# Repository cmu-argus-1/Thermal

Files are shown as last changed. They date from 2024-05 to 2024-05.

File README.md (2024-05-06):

# Thermal
All files relating the thermal management of Argus-1 are located here. The following files can located within this repository:
* Thermal Desktop setup and login information
* Thermal Desktop help manuals and tutorials
* Argus-1 Thermal Desktop files
* Argus-1 TVAC test plan
* Argus-1 thermal management system CAD files
* Argus-1 thermal strap DXF files

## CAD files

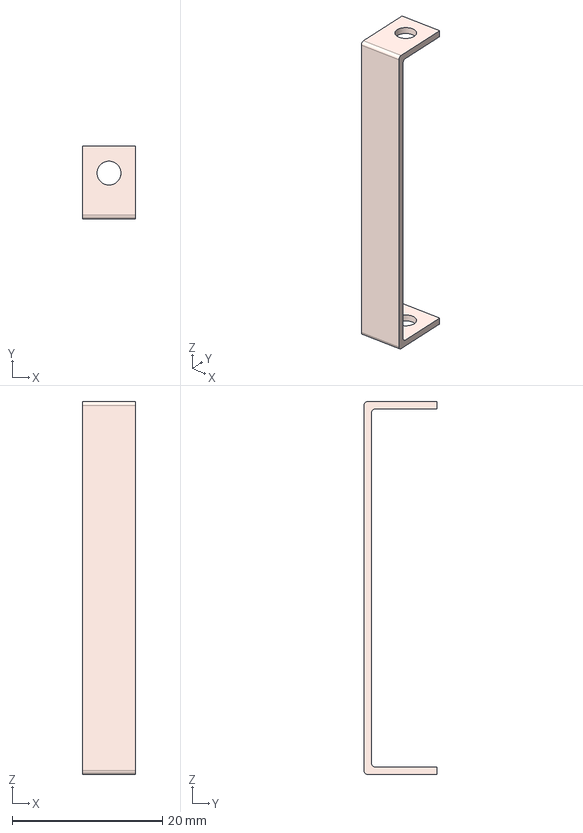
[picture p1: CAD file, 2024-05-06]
Thermal Strap Short.step
7.00 x 9.70 x 49.6 mm

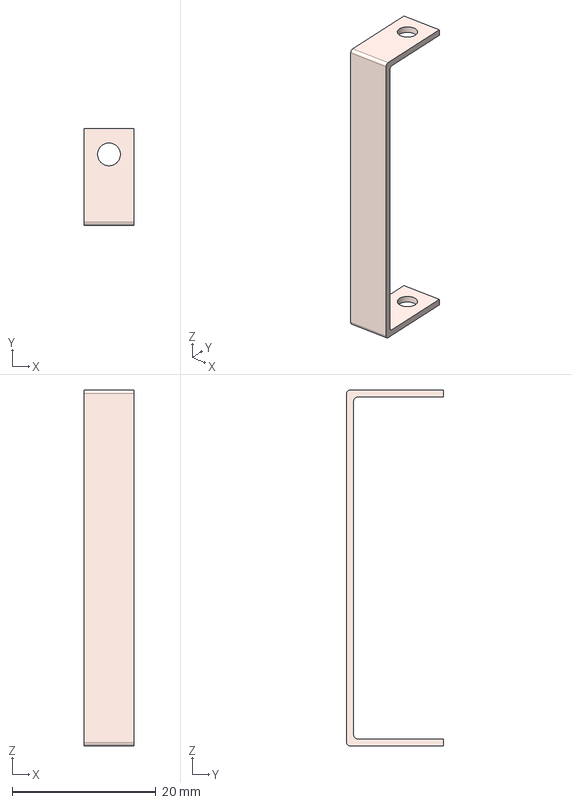
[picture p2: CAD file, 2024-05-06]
Thermal Strap Long.step
7.00 x 13.5 x 49.6 mm

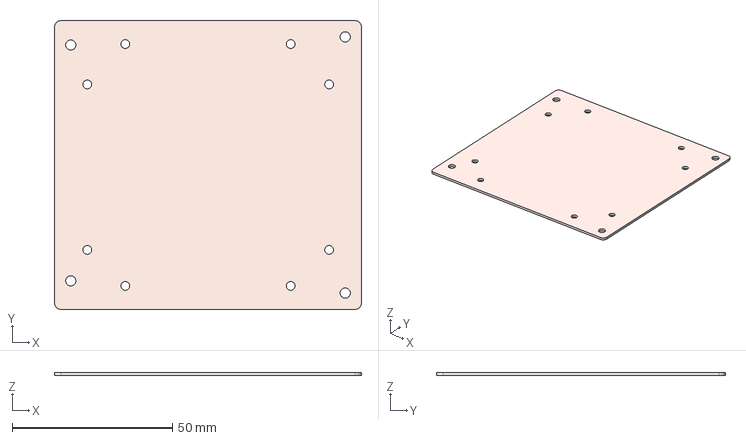
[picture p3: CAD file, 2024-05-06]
Jetson Thermal Sink Board.step
95.9 x 90.2 x 1.00 mm

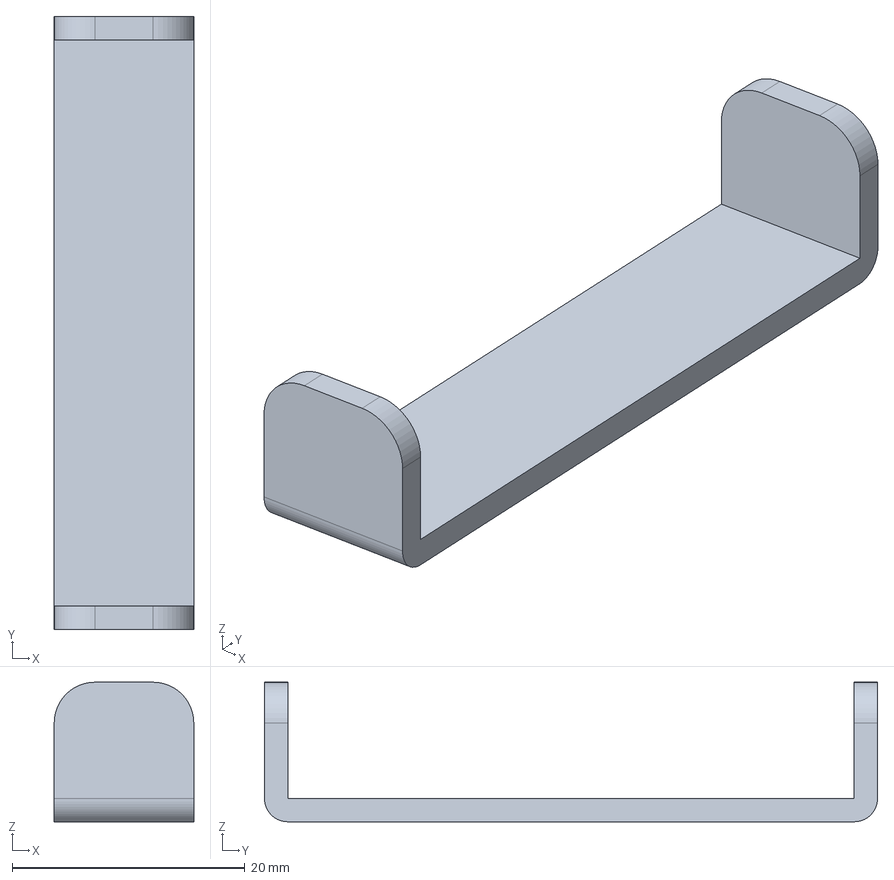
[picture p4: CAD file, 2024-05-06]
Copper Strap.step
12.0 x 52.7 x 12.0 mm

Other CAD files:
TDD_Test_Drawing.dwg
CubeSat_v1.dwg

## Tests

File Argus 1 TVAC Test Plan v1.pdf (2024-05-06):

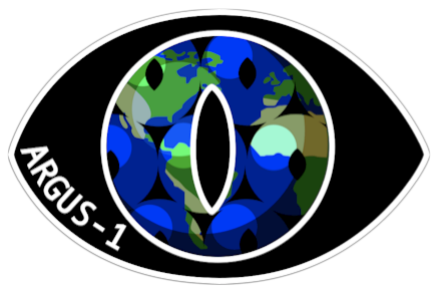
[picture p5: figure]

# Argus-1

# Camera Module Endurance

&

# Jetson Thermal Management TVAC Test Plan

Carnegie Mellon University 5000 Forbes Ave
Pittsburgh, PA 15213
Revision | Release Notes Author | Release Date
A | Initial Release Colton Amos | 4/11/2024

Revision | Title | Release Date | Page
A | Camera Module and Jetson TVAC Test Plan | 4/11/2024 | 2 of 19

Table of Contents
Page No.
1.0 Purpose and Scope | 3
2.0 (https://docs.google.com/document/d/1Rzob_Sl6tvCRn7rMNGoZeeShy_QEGQafTcheLyu6lXM/edit) Involved Personnel | 5
3.0 Test Articles | 6
4.0 Facilities | | | 7
5.0 Test Procedures | 11
6.0 Results & Conclusions | 16
7.0 Literature and Relevant Documents | 22

A | Camera Module and Jetson TVAC Test Plan | 4/11/2024 | 3 of 19

### 1.0 Purpose and Scope

This test plan verifies the endurance capabilities of a selected camera unit and its consequent resistance to thermal distortion in its lenses and mounted PCB. Furthermore, this plan will also investigate the proficiency of a proposed thermal management system for an on board Jetson unit. The performance of a copper vs aluminum thermal sink board will be compared utilizing a copper thermal strap to the aluminum chassis. These results and their respective conductances will then be incorporated into a protoflight thermal model.

1.1 Requirements Table

Table 1: Requirements
ID | Title | Description | Information Learned in this Version
THR-01 | Survival Temperature Regulation | The thermal system shall maintain temperatures in accordance with the ThEL survival temperatures during orbit without operating high-risk avionics components.
THR-02 | Operation Temperature Regulation | The thermal system shall maintain temperatures in accordance with the ThEL operating temperatures during orbit that involve high-risk components being on.
THR-17 | Thermal Model Correlation | Argus-1 shall have a thermal model that is correlated to within 5% temperature accuracy in K.
THR-18 | Thermal Vacuum Survivability | The thermal system shall use components that will survive the vacuum conditions of low Earth orbit.

A | Camera Module and Jetson TVAC Test Plan | 4/11/2024 | 4 of 19

### 2.0 Involved Personnel

Table 2: Personnel
Name | Role | Contact Information
Colton Amos | Thermal Lead | camos@andrew.cmu.edu
Ashley Kline | Mechanical Engineer | ankline@andrew.cmu.edu
Allison Weller | Mechanical Engineer | ahweller@andrew.cmu.edu
Sankalp Chopkar | Mechanical Engineer | schopkar@andrew.cmu.edu
Rohit Bangal | Avionics Engineer | rbangal@andrew.cmu.edu
Elakhya Nedumaran | Payload Engineer | enedumar@andrew.cmu.edu
Paulo Fisch | Thermal/Mechanical Advisor | pfisch@andrew.cmu.edu
Zach Manchester | Professor | zmanches@andrew.cmu.edu
Brandon Lucia | Professor | blucia@andrew.cmu.edu
Chuck Whittaker | Supervisor | warrenw@andrew.cmu.edu

A | Camera Module and Jetson TVAC Test Plan | 4/11/2024 | 5 of 19

### 3.0 Test Articles

The TVAC test will be primarily testing two articles. A fully assembled Arducam camera module including its two mounted PCB’s, its camera housing and its camera lens. A CAD representation of this article can be found below:

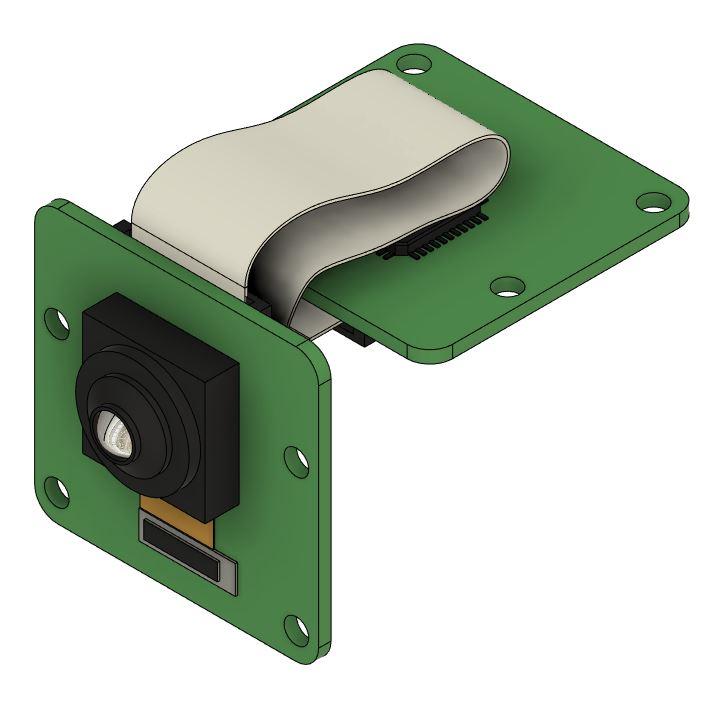
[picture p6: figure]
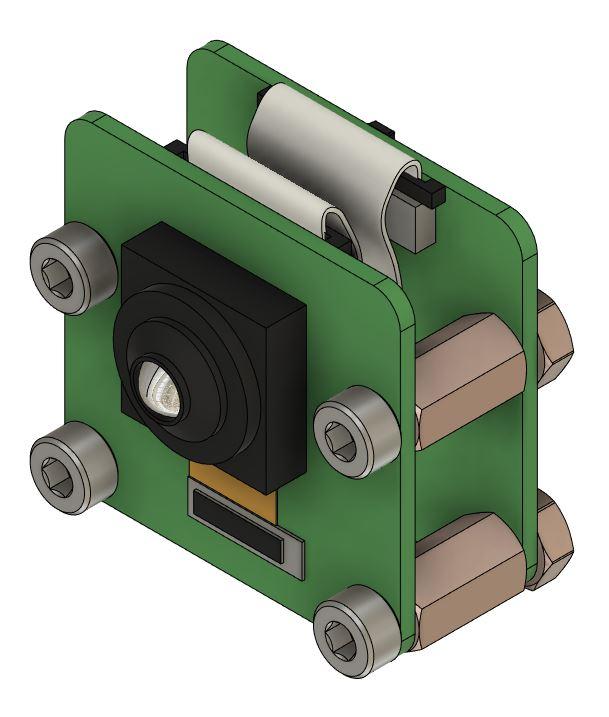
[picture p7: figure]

The second test article will be sub assembly of the thermal management system for the Jetson Module. This sub assembly includes: the chassis frame and legs, M3 PC104 rods, 4 copper thermal straps, a copper and aluminum thermal sink board, a Jetson Module, Jetson carrier board, thermal gap pad, and all associated M3 mounting hardware. Abbreviated assembly instructions can be found in Table 4: Test Setup. A CAD representation of the thermal management system can be found below:

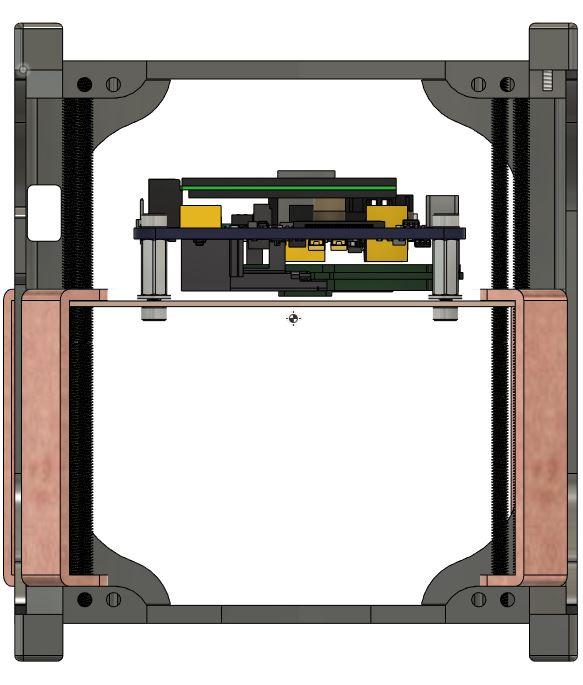
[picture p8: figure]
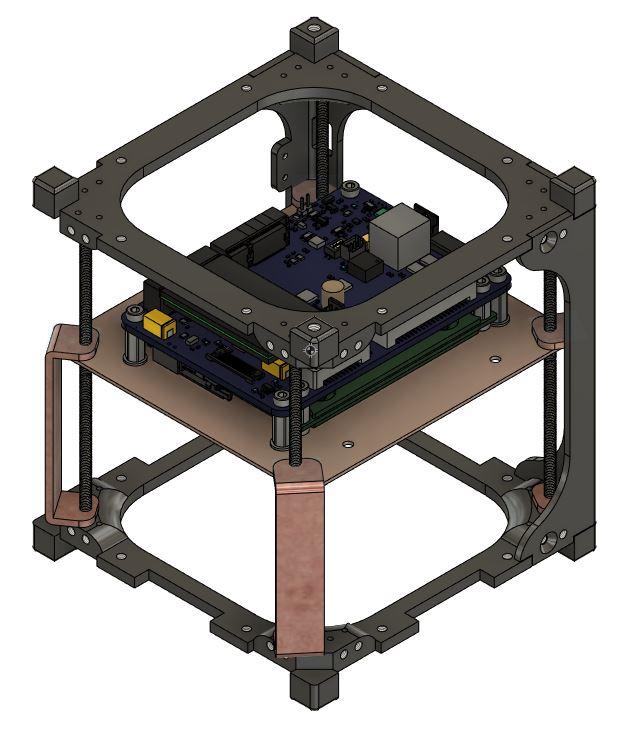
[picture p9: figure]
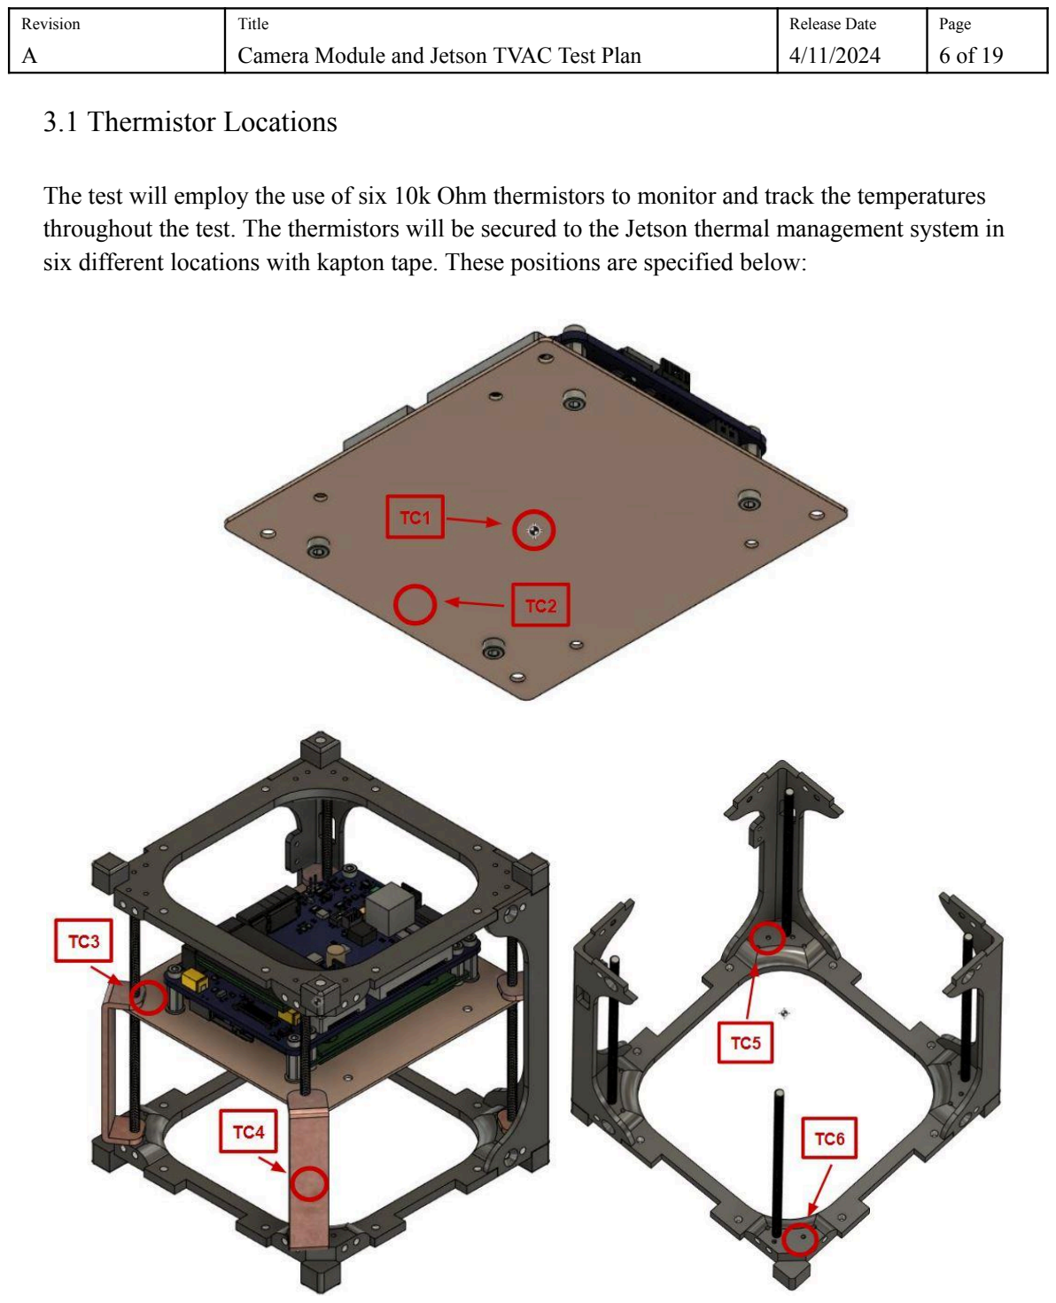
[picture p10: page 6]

A | Camera Module and Jetson TVAC Test Plan | 4/11/2024 | 6 of 19

3.1 Thermistor Locations

The test will employ the use of six 10k Ohm thermistors to monitor and track the temperatures throughout the test. The thermistors will be secured to the Jetson thermal management system in six different locations with kapton tape. These positions are specified below:

A | Camera Module and Jetson TVAC Test Plan | 4/11/2024 | 7 of 19

### 4.0 Facilities

The test will happen in the Robotics Institutes’s vacuum chamber, located in the Planetary Robotics Laboratory High Bay on floor 1 of Gates Center.

### 5.0 Test Procedures

5.1 Summary

Table 3: Summary
Description:

This test assesses the effects of thermal dilation of a camera unit and a Jetson computing unit under TVAC conditions. The camera module’s PCB and lens resistance to thermal distortion are going to be measured by placing a fully assembled camera module onto the bottom of the vacuum chamber’s cryogenic shroud, which will cool the camera module to a set temperature. The temperature profile and thermal management system of a Jetson module are going to be tested by placing an assembled chassis mounted Jetson unit and thermal sink board onto the bottom of the vacuum chamber’s cryogenic shroud, which will cool the chassis and Jetson unit to a set temperature. The temperature time-histories of the Jetson module will be used in simulations to back calculate its conductances with the thermal sink board. The temperature profile and power output will also be recorded to get an accurate model of Jetson operational conditions.

Pass Criteria:

The camera module shows minimal distortion post TVAC conditions and maintains the same image quality as pre test calibrated images. Temperature profile across the Jetson module stays within supplier specified survival and operating temperature bounds throughout the duration of the test. The proposed thermal management system shows effective heat transfer to the chassis.

Data Products (data to be collected during test):

Temperature time histories of the camera pcb, Jetson module, thermal sink board, chassis frame and vacuum chamber. The pressure time histories of the vacuum chamber shall be collected. The power outputs of the Jetson module during GPU burn.

Test Articles:

Part Number: | Description: | Revision:
B0305 | Arducam 12MP IMX708 camera module

A | Camera Module and Jetson TVAC Test Plan | 4/11/2024 | 8 of 19
900-13767-0000-000 | Jetson Orin module
| Jetson Orin Carrier Board
Custom | Copper thermal sink board
Custom | Aluminum thermal sink board
Custom | Copper thermal straps
2242235 | Thermal Gap Pad
a21072000ux0246 | M3 PC104 threaded rods
Custom | Aluminum Chassis (top, bottom and 4 legs)
90592A085 | M3 PC104 mounting hex nuts
92125A125 | M3 Chassis mounting hardware
93655A093 | Jetson Orin mounting standoffs

Test Equipment:

ID: | Description: | Calibration Date
| Vacuum Chamber
| Agilent Thermocouple DAQ Module
| 10k Ohm Thermistors
| Polyimide Heater
| BD Lab Supply (for lamps and dot projectors)
| Sorensen DCS20 Lab Supply (For Spacely)
| Arduino Uno Microcontroller
| MAX31855 Thermocouple Breakout
| Sensata Crydom CMX600D10 Solid State Relay
| HDMI Compatible Monitor (with power cable and HDMI cable)
| USB keyboard and mouse

A | Camera Module and Jetson TVAC Test Plan | 4/11/2024 | 9 of 19

5.2 Test Setup
Table 4: Test Setup
Procedure Step: | Diagrams / Descriptions:
1. Calibrate camera, record resulting camera calibration (if this was already done, no need to redo) | Confirm with Payload that the selected camera has been calibrated before the test. Points of communication are Kyle McClearly and Elakhya Nedumaran.
2. Clean PCB edges, camera housing, and camera lens | Ensure that isopropyl alcohol is used or a sufficiently sensitive cleaning solvent
3. Clean chassis legs, top and bottom | Ensure that isopropyl alcohol is used or a sufficiently sensitive cleaning solvent
4. Clean M3 PC104 rods threads | Ensure that isopropyl alcohol is used or a sufficiently sensitive cleaning solvent
5. Clean M3 PC104 mounting hardware, Jetson Module standoffs | Ensure that isopropyl alcohol is used or a sufficiently sensitive cleaning solvent
6. Clean copper thermal straps | Ensure that isopropyl alcohol is used or a sufficiently sensitive cleaning solvent
7. Clean copper and aluminum thermal boards | Ensure that isopropyl alcohol is used or a sufficiently sensitive cleaning solvent
8. Clean Jetson Module and corresponding carrier board | Ensure that isopropyl alcohol is used or a sufficiently sensitive cleaning solvent
9. Screws all 4 legs into lower chassis frame using M3 hardware | Ensure that all hardware is torque is manufacture specifications accurately replicating flight conditions
10. Screw all 4 PC104 rods into lower chassis | Ensure that all hardware is torque is manufacture specifications accurately replicating flight conditions
11. Place lower half of thermal strap onto each PC104 rod with corresponding M3 hex nut | Ensure full contact is made with the lower chassis frame and the thermal strap (picture for reference)
12. Place thermal sink board onto all PC104 rods with an M3 hex nut below the board

A | Camera Module and Jetson TVAC Test Plan | 4/11/2024 | 10 of 19
13. Place upper half of the thermal strap onto each PC104 rod with an M3 hex nut above the strap | Ensure full contact is made with the lower thermal sink board and the thermal strap (picture for reference)
14. Secure the lower portion of the thermal strap to the lower chassis with the M3 hex nut | Ensure full contact is made with the lower chassis frame and the thermal strap (picture for reference)
15. The set the preferred Z-axis height of the thermal sink board and secure in place with the M3 hex nut below the board and the M3 hex nut above the thermal strap (This action sandwiches the thermal strap onto the thermal board while simultaneously setting the Z-axis height) | For reference the thermal sink board should be ~ 42 mm in z height from the lower chassis frame (picture for reference)
16. Align the Jetson Module and the carrier board to the thermal sink board to identified region for thermal gap pad | (picture for reference)
17. Apply thermal gap to thermal sink board ensuring full coverage of the GPU is established | Ensure the entire surface area of the GPU unit is covered by the thermal gap pad. Clean surfaces with isopropyl alcohol before applying the gap pad.
18. Use the carrier board standoffs to mount the carrier board to thermal sink board | Ensure sufficient contact is made with the thermal gap pad
19. Place the upper portion of the chassis onto the PC104 rods and align with the 4 legs | Ensure upper frame PC104 mounting holes are unthreaded for ease of installation
20. Screws all 4 legs into upper chassis frame using M3 hardware | Ensure that all hardware is torque is manufacture specifications accurately replicating flight conditions
21. Take test articles to vacuum chamber in sealed bag
22. Open vacuum chamber lid and clamp test articles ON THE SIDE OF THE SHROUD CLOSEST TO VACUUM

A | Camera Module and Jetson TVAC Test Plan | 4/11/2024 | 11 of 19

CHAMBER PLATFORM.

23. Mount thermocouples to the chassis frame, thermal sink board, and Jetson carrier board. | Use kapton tape small piece of gap pad to firmly secure thermocouples to chassis frame, thermal sink board, and Jetson carrier board
24. Connect thermocouples to the DAQ
module and to the microcontroller. | THE THERMOCOUPLE CONNECTED TO THE CONTROL SYSTEM NEEDS TO BE MOUNTED TO THE SHROUD OR THE CONTROL SYSTEM WILL NOT FUNCTION PROPERLY. IF THIS STEP IS NOT FOLLOWED CORRECTLY, THE ENTIRE TEST WILL NOT BE VALID.
| INCORRECT THERMOCOUPLE MOUNTING WILL ALSO NEGATIVELY IMPACT PERFORMANCE. PAY SPECIAL ATTENTION TO CREATING A PROPER THERMAL BOND FOR THE THERMOCOUPLE AND THE RADIATOR
25. Connect lamp to wires leading to BD power sources and Spacely to Sorensen power source. | Connect dot projectors IN PARALLEL. Set Spacely power supply to 15V and limit current to 2A before connecting. Set BD power source to 5V
26. Plug power supplies into wall socket
27. Turn on lab supplies and check lamp functionality
28. Connect to the Spacely | Connect a monitor, keyboard, and mouse to

A | Camera Module and Jetson TVAC Test Plan | 4/11/2024 | 12 of 19
| the spacely
29. Verify the correct git branch is selected for the test | ~~Not sure what git branch to use
30. Verify the Jetson is powered on and connected to the correct ports | Verify commands and outputs
31. Verify that the code is compiled | Ensure code compiled with no errors
32. Confirm that sufficient disk space exists | Confirm that at least 2GB of space is free on the system (2GB will be sufficient so long as the test runs for less than 10 hours). If needed, the build directories of the other workspaces can be cleared to make space check with the workspace owners first to make sure they don’t need any files stored in build (especially images in /cf)
33. Start Jetson GPU burn operation cycle
34. Verify Jetson is running and performing test functions | Check power output and outputs of GPU burn to ensure results are what is expected
35. Disconnect the monitor, mouse and keyboard from the Spacely | Do not disconnect the power or the cameras from the spacely. NOT REQUIRED IF USING SSH
36. Connect chamber shroud line to Liquid Nitrogen Tank. Open tank valve. | FOLLOW SAFETY PROCEDURES FOR LIQUID NITROGEN. WEAR GLOVES AND A FACE SHIELD. ENSURE NO UNPROTECTED PERSONNEL IS CLOSE TO LN2 TANK BEFORE CONNECTING LINES AND

A | Camera Module and Jetson TVAC Test Plan | 4/11/2024 | 13 of 19
| OPERATING VALVES
37. Turn on thermocouple and DAQ modules. Verify temperature readings. Input desired temperature profile. | Do not set temperature drop ramps to inclinations steeper than 2min/oC
38. Close the vacuum chamber lid

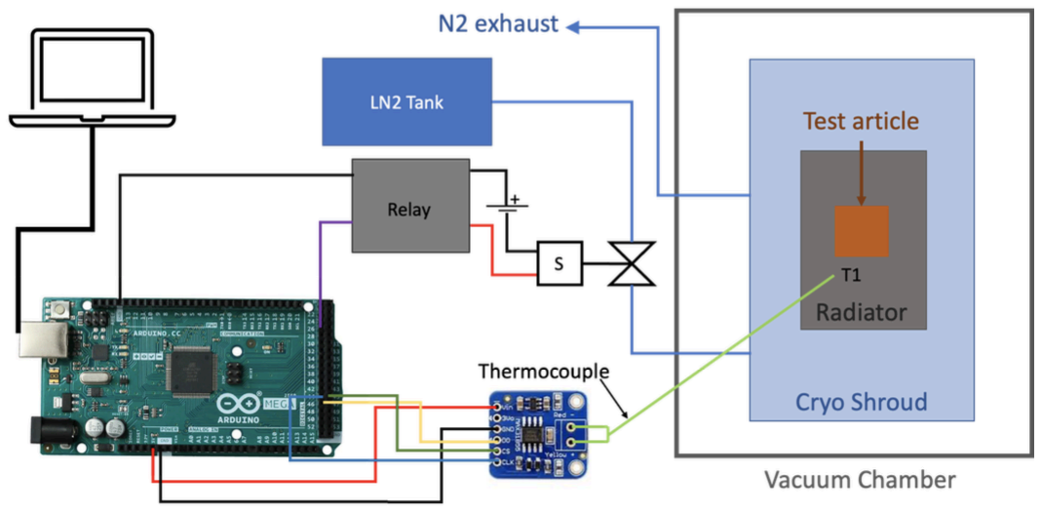
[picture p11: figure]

5.3.1 Test Procedures
Table 5: Test Procedures
Procedure Step: | Expected Result: | Actual Result:
1. Record the current time as “post closing TVAC Chamber lid” | Time noted in spreadsheet (link here) | ___ Pass ___ Other Explain:
2. Wait 15 minutes, allowing the Jetson to continually operate in a normal state with the GPU burn activated. | Check expected outputs of GPU burn, confirm with Payload liaison | ___ Pass ___ Other

A | Camera Module and Jetson TVAC Test Plan | 4/11/2024 | 14 of 19
| | Explain:
3. Continually record the wattage of the Jetson Module during the entire test. First data collection shall begin must the GPU has begun. | Wattage noted in spreadsheet (link here) | ___ Pass ___ Other Explain:
4. Record the current time as “pre activating vacuum chamber pumps” | Time noted in spreadsheet (link here) | ___ Pass ___ Other Explain:
5. Activate vacuum chamber pumps. | Pressure should be less than 10e-2 Torr | ___ Pass ___ Other Explain:
6. Wait for the vacuum chamber to get to hard vacuum (pressures lower than 10^-2 Torr) | Pressure should be less than 10e-2 Torr | ___ Pass ___ Other Explain:
7. Record the current time as “post hard vacuum achieved” | Time noted in spreadsheet (link here) | ___ Pass ___ Other Explain:
8. Wait 15 minutes, allowing the Jetson to continually operate in a normal state. | Check expected outputs of GPU burn, confirm with Payload liaison | ___ Pass ___ Other Explain:
9. Record the current time as “pre activating dot projectors and shroud thermal control” | Time noted in spreadsheet (link here) | ___ Pass ___ Other Explain:
10. Record the wattage of the Jetson | Wattage noted in | ___ Pass

A | Camera Module and Jetson TVAC Test Plan | 4/11/2024 | 15 of 19
during the GPU burn. | spreadsheet (link here) | ___ Other Explain:
11. Turn on dot projectors. If possible, confirm via thermocouple readings that the dot projectors are indeed active. | Dot projectors active | ___ Pass ___ Other Explain:
12. Activate shroud thermal control system. | Temperatures follow the specified temperature curve to 10% divergence | ___ Pass ___ Other Explain:
13. Record the current time as “post shroud activation” | Time noted in spreadsheet (link here) | ___ Pass ___ Other Explain:
14. Record the wattage of the Jetson during the GPU burn. | Wattage noted in spreadsheet (link here) | ___ Pass ___ Other Explain:
15. Perform inspections of the test articles for damage every 30 minutes. Overshoots larger than 15°C are expected when ramping down. | Thermocouples, Jetson module, and shroud temperature control system functioning normally | ___ Pass ___ Other Explain:
16. Check data every 10 to 15 minutes. Allow the shroud system to oscillate slowly around the reference temperature. Look for big jumps in temperature or current readings that might indicate some sort of thermocouple joint failure or test article failure. | Thermocouples, Jetson module, and shroud temperature control system functioning normally | ___ Pass ___ Other Explain:

A | Camera Module and Jetson TVAC Test Plan | 4/11/2024 | 16 of 19
17. Deactivate the solenoid after two to three hours or if temperatures get close to -40°C. | DEACTIVATE SOLENOID IF TEMPERATURES DROP TOO MUCH TO AVOID COMPONENT FAILURE | ___ Pass ___ Other Explain:
18. Let the test articles cool until temperature readings stabilize and oscillate with the shroud temperature. | Jetson module shall follow desired temperature profile | ___ Pass ___ Other Explain:
19. Record the current time as “start of desired thermal state for test” | Time noted in spreadsheet (link here) | ___ Pass ___ Other Explain:
20. When the camera module and Jetson module is at desired equilibrium temperature, maintain this state for 30 minutes to fully capture thermal management capabilities of the system. Continue checking data. | Jetson module functional. Temperature data and wattage data is continually being recorded | ___ Pass ___ Other Explain:
21. Record the current time as “end of desired thermal state for test” | Time noted in spreadsheet (link here) | ___ Pass ___ Other Explain:
22. Record the wattage of the Jetson during the GPU burn. | Wattage noted in spreadsheet (link here) | ___ Pass ___ Other Explain:
23. Remove solenoid power cord from socket and close LN2 tank valve. DO NOT TOUCH THE LN2 TANK VALVE UNTIL SOLENOID IS PROPERLY POWERED OFF | FOLLOW SAFETY PROCEDURES FOR LIQUID NITROGEN. WEAR GLOVES AND | ___ Pass ___ Other Explain:

A | Camera Module and Jetson TVAC Test Plan | 4/11/2024 | 17 of 19
| A FACE SHIELD. ENSURE NO UNPROTECTED PERSONNEL IS CLOSE TO LN2 TANK BEFORE CONNECTING LINES AND OPERATING VALVES.
24. Vent the vacuum chamber to the atmospheric pressure following MEC-0275 procedures. | Vacuum chamber vented to atmospheric pressure | ___ Pass ___ Other Explain:
25. Deactivate the Jetson Module and ensure the entire system is powered down. | | ___ Pass ___ Other Explain:
26. Open the vacuum chamber lid. | | ___ Pass ___ Other Explain:
27. Remove the thermocouples from the test articles. Unplug heaters from the power supply. Check for integrity of full data acquisition. | | ___ Pass ___ Other Explain:
28. Take the test articles out of the vacuum chamber in sealed bags. | | ___ Pass ___ Other Explain:
Test Completed By: | Date:

A | Camera Module and Jetson TVAC Test Plan | 4/11/2024 | 18 of 19

5.3.2 Data Analysis Procedures
Table 6: Post Test Data Analysis
Procedure Step: | Expected Result: | Actual Result:
1. Process and compile all recorded temperatures from thermocouples and Jetson module. Separate based on test article and temperature reading location. | Data compiled in test spreadsheet (link here) | ___ Pass ___ Other Explain:
2. Align all recorded temperatures with their respective time stamps. | Align and clean data in spreadsheet | ___ Pass ___ Other Explain:
3. Align recorded wattages with the indicated time stamps. | Align and clean data in spreadsheet
4. Highlight the following milestone timestamps as recorded during the test: “post closing TVAC Chamber lid”, “pre activating vacuum chamber pumps”, “post hard vacuum achieved”, “pre activating dot projectors and shroud thermal control”, “post shroud activation”, “start of desired thermal state for test”, and “end of desired thermal state for test”. | Align and clean data in spreadsheet | ___ Pass ___ Other Explain:
Date Compile Completed By: | Date:

5.4 Safety Concerns

- Only trained personnel are authorized to operate the vacuum chamber
- Exposure to electricity from heaters and lab power supplies
- Exposure to LN2. Only trained and authorized personnel can operate the LN2 shroud
- Be cautious and aware of extreme temperatures present on the test articles

A | Camera Module and Jetson TVAC Test Plan | 4/11/2024 | 19 of 19

### 6.0 Results & Conclusions

6.1 Special Test Information

This test requires the use of a control system to regulate mock radiator temperatures by activating the shroud LN2 line. Contact Paulo Fisch (pfisch@andrew.cmu.edu) or Chuck Whittaker (warrenw@andrew.cmu.edu) if you have any questions. Each board will require specific ports for communication in the chamber. Verify with Avionics, Payload, and Mechanical teams

6.2 Test Failures & Corrective Actions

6.3 Unaccomplished Tasks & Recommended Retests

### 7.0 Literature & Relevant Documents

MR-MEC-0275: Vacuum Chamber Operation Guidelines
